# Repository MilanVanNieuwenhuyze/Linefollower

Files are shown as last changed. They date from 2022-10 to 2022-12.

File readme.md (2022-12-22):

# LineFollower
<br />
lege repository die je als template kan gebruiken om een eigen repository te starten voor uw linefollower project
<br />
<br />
(https://user-images.githubusercontent.com/114940508/209196277-916155c1-5bc2-4fb1-94a1-3e10acf964d6.jpg)

<br />
<br />
  
## specifications
<br />
microcontroller: Arduino UNO
<br />
motors: DC 50:1 gearmotor
<br />
h-bridge: DRV8835
<br />
sensors: QTR-8A
<br />
batteries: 2x Lithium batterijen 3.7V 3200 mAh
<br />
wireless communication: HC-05
<br />
distance sensor - motors: 8.6 cm
<br />
weight: 0.219 kg
<br />
speed: 0.546 m/s
<br />

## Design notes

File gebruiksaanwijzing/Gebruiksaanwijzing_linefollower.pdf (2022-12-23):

Jarno Calmeyn & Milan Van Nieuwenhuyze

## Gebruiksaanwijzing

Voorzie de linefollower van stoom:

Optie 1: met de Lithium batterijen

- Maak dat de Robot losgekoppeld van de computer
- Plaats de twee opgeladen lithium batterijen in de houder achteraan op de Robot
- Zet de schakelaar zodat de led brandt
- De Arduino is nu voorzien van stroom

Optie 2: kabel via computer

- Controleer dat het ledlampje niet brand (haal voor de zekerheid de batterijen uit de Robot)
- Verbind de Robot met de computer via de meegeleverde kabel (USB B)
- Het ledlampje zal branden en de arduino is nu voorzien van stroom

Opstarten van de Linefollower

- Koppel de robot los van de USB type B kabel
- Plaats (indien nog niet aanwezig) de twee lithium batterijen in de daar voor voorziene houder volgens de instructies aangegeven op de houder (plus aan plus en min aan min)
- Zet de schakelaar aan zodanig de led brandt
- Zet de robot op het zwarte vlak op het parcour
- Kalibreer zwart via de Seriële monitor ‘Start calibrating black’
- Zet de robot op het wit gedeelte op het parcour
- Kalibreer wit via de Seriële monitor ‘start calibrating white’
- De robot is nu klaar voor gebruik

Rijden met de linefollower

- Plaats de robot op het parcour op de startplaats
- Druk op de start/stop knop
- De robot zal de lijn op het parcour beginnen volgen
- Voor te stoppen pak je de robot van het parcour (hij zal automatisch stoppen met rijden)

Uitschakelen van de Linefollower

- Zet de schakelaar zodanig de led niet brandt
- Haal voor de zekerheid de lithium batterijen uit de houder

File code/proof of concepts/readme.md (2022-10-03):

# Proof of Concepts

Een proof of concept is een combinatie van minimale hard- en software om eenvoudig aan te tonen dat iets werkt.  
Proof of concepts kunnen enerzijds als eerste poging dienen om een bepaald onderdeel van het project werkend te krijgen. Anderzijds kunnen ze tijdens het debuggen van het finale project dienen als test om eventuele hardware problemen te elimineren bij onduidelijke problemen.
<br />  
<br />
Een proof of concept bestaat uit
* een elektronisch schema (indien van toepassing)
* minimale code om de voorop gestelde zaken te demonstreren
* minimale uitleg / aandachtspunten
<br />
De elektronische schakelingen van de proof of concepts komen bij voorkeur overeen met deze van de uiteindelijke linefollower, zodat de code zonder aanpassingen op het finale project kan draaien.

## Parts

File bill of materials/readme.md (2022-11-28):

## bill of materials
<br />

|volgnummer|naam|omschrijving|nieuw/recup|kostprijs/stuk|aantal|subtotaal|
|---|----|---|---|---|---|---|
| 1|  Arduino uno  |  De Arduino UNO zal er voor zorgen dat we alle onderdelen kunnen aansturen aan de hand van een geschreven code in het programma Arduino IDE |  recup | €0,00 |  1 |  1 |
|2|Batterijhouder (2 x 18650)|In deze houder kunnen we de 2 batterijen plaatsen|recup|€0,00|1|1|
|3|Batterij (2 x 18650) + oplader|Deze batterijen zullen alle onderdelen van voeding voorzien|recup|€0,00|1|1|
|4|DC 50:1 gearmotor|De motoren zullen ervoor zorgen dat de wielen beginnen draaien|nieuw|€18,35|2|€36,70|
|5|H-brug (DRV8835)|De H-brug zal de draaizin en snelheid van de motoren regelen|nieuw|€7,15|1|€7,15|
|6|Array sensor (QTR-8A)|De sensor zal de zwarte lijn op het parkour detecteren, zo zal de robot deze lijn blijven volgen|nieuw|€11,5|1|€11,5|
|7|Bluetooth module (HC-05)|De bleutooth module zal er voor kunnen zorgen dat we draadloos met de robot kunnen communiceren, dit aan de hand van een app op de gsm|nieuw|€6,85|1|€6,85|
|8|Polulu wiel (40 x  7) zwart|Wielen, hierdoor zal de robot kunnen rijden op een oppervlakte|nieuw|€2,48|2|€4,96|
|9|Gearmotor bracket|Houdertjes die aan de grondplaat worden bevestigd, deze zorgen ervoor dat de motoren op hun plaats blijven|nieuw|€1,98|2|€3,96|
|10|Tuimelschakelaar|Schakelaar voor de robot van voeding te voorzien|recup|€0,00|1|€0,00|
|11|Dupont draadjes|Verbinden van ingangen en uitgangen|recup|€0,00|15|€0,00|
|12|Drukknop|Zet het karretje aan/uit|recup|€0,00|1|€0,00|
|13|Led|Geeft aan of de voeding aan staat|recup|€0,00|1|€0,00|
|14|Bouten|Houdt de onderdelen op zijn plaats|recup|€0,00|10|€0,00|
| | | | | |Totaal |€71,10 |

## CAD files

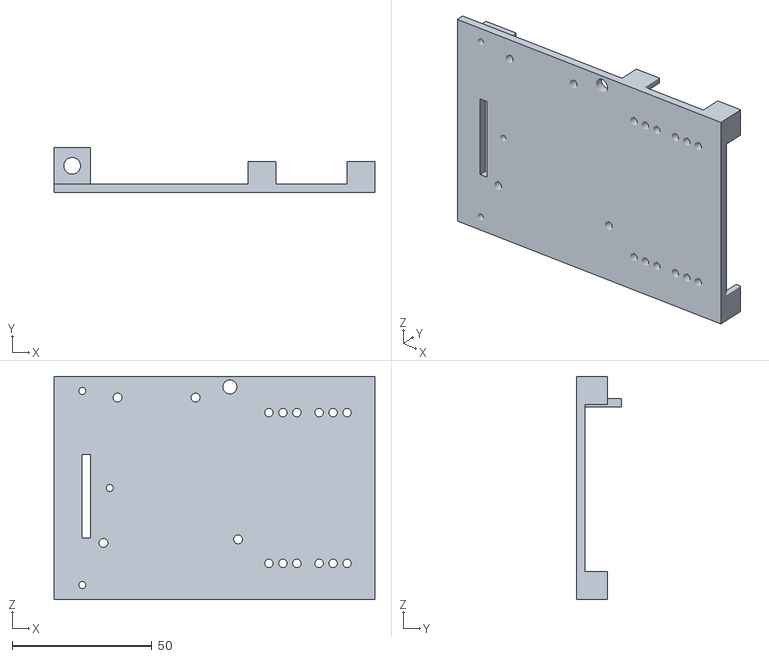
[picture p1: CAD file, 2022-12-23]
technische tekeningen/mechanisch/Bodemplaat.STL
115.0 x 16.0 x 80.0

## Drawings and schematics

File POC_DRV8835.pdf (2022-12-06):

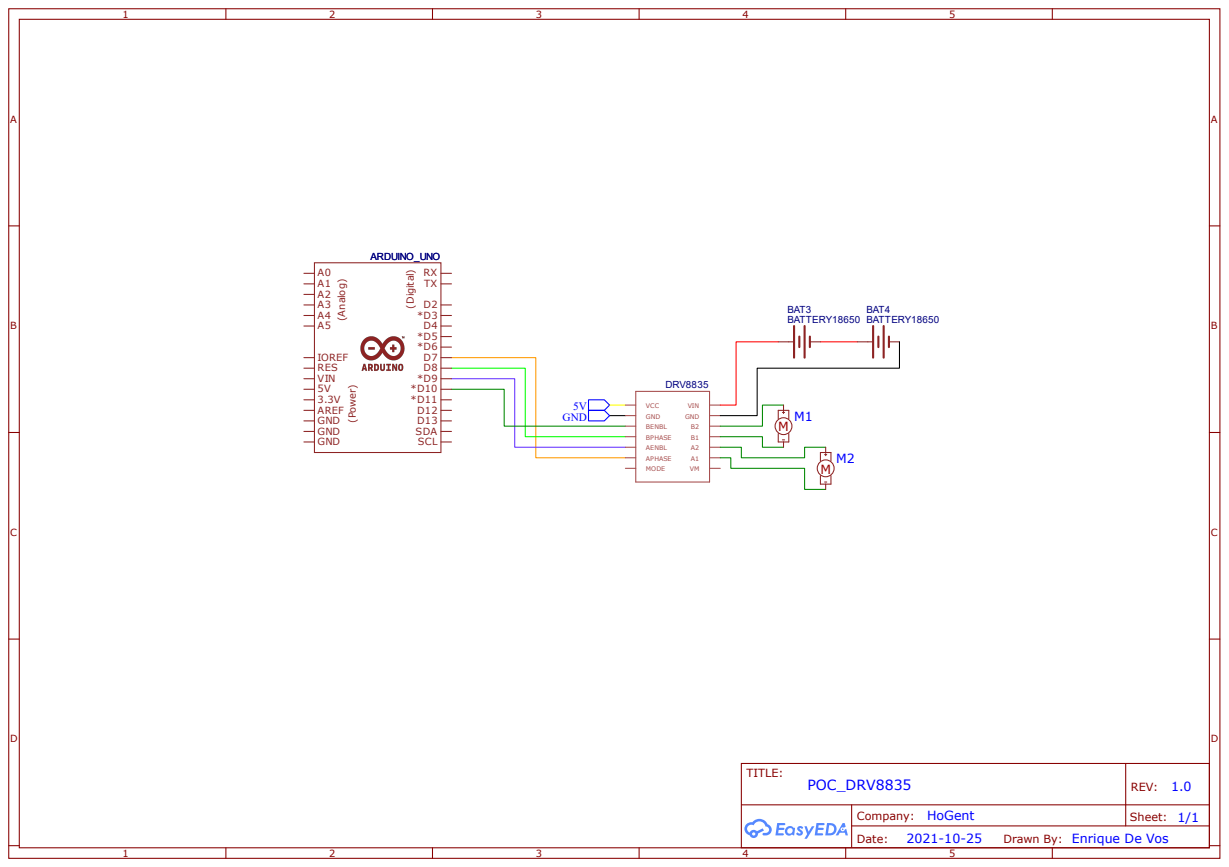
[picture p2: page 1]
TITLE:; POC_DRV8835; REV: 1.0; Date:; Sheet: 1/1; Company: HoGent; ARDUINO_UNO; GND; DRV8835; GND BENBL BPHASE; MODE; VCC; VIN; AENBL; APHASE; ARDUINO_UNO RX TX; RES; AREF GND GND GND; IOREF; SDA SCL; (Analog); (Digital); (Power); BATTERY18650; BAT3; BAT4

Drawn By: Enrique De Vos

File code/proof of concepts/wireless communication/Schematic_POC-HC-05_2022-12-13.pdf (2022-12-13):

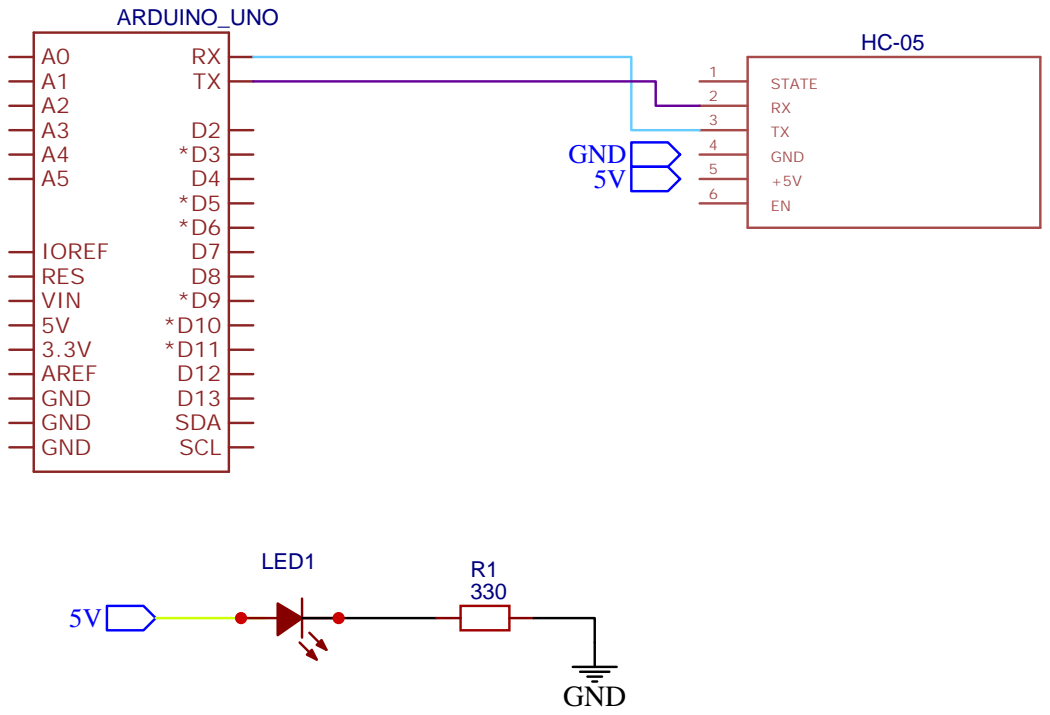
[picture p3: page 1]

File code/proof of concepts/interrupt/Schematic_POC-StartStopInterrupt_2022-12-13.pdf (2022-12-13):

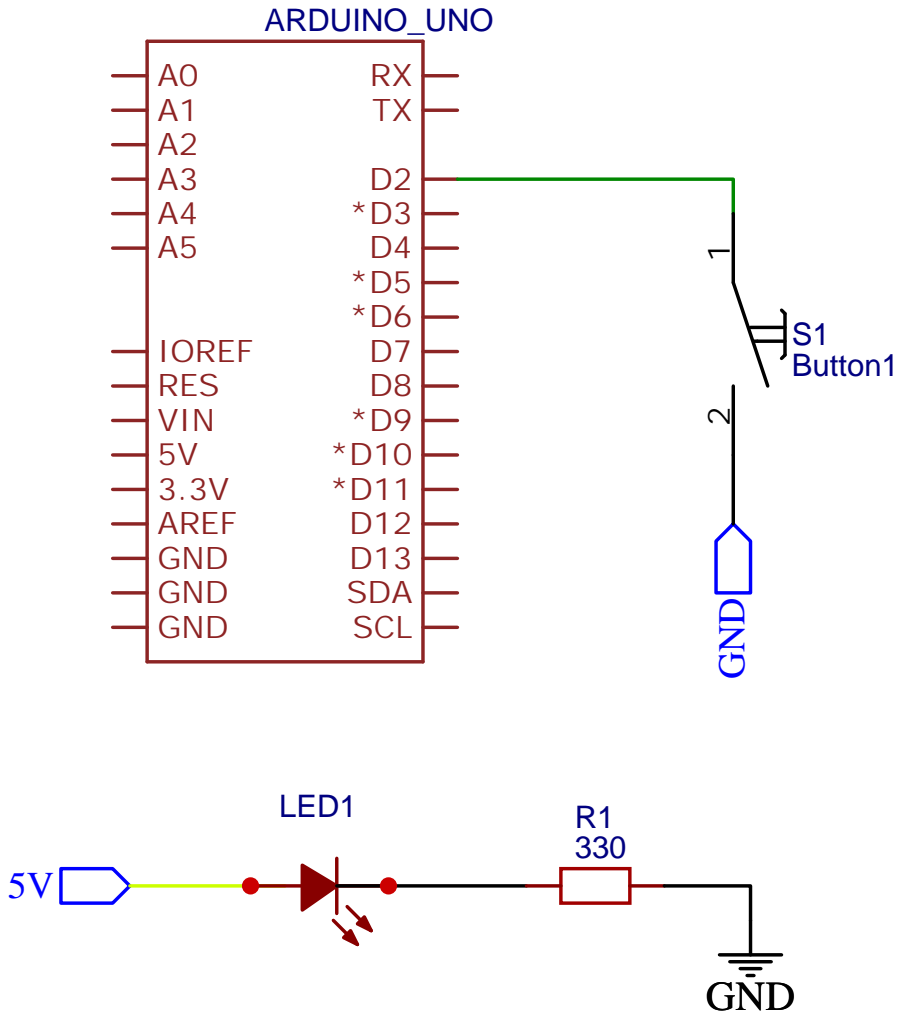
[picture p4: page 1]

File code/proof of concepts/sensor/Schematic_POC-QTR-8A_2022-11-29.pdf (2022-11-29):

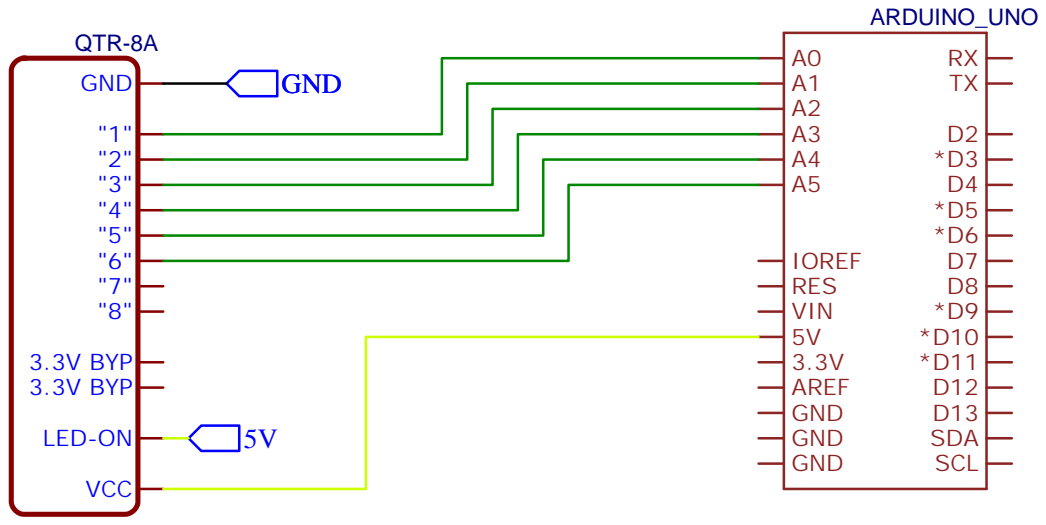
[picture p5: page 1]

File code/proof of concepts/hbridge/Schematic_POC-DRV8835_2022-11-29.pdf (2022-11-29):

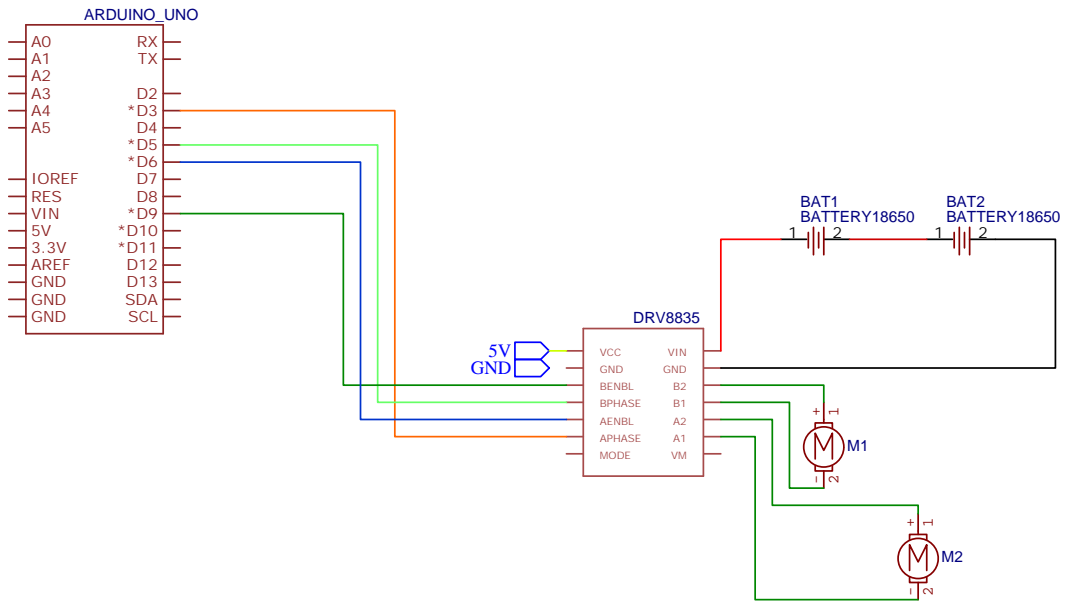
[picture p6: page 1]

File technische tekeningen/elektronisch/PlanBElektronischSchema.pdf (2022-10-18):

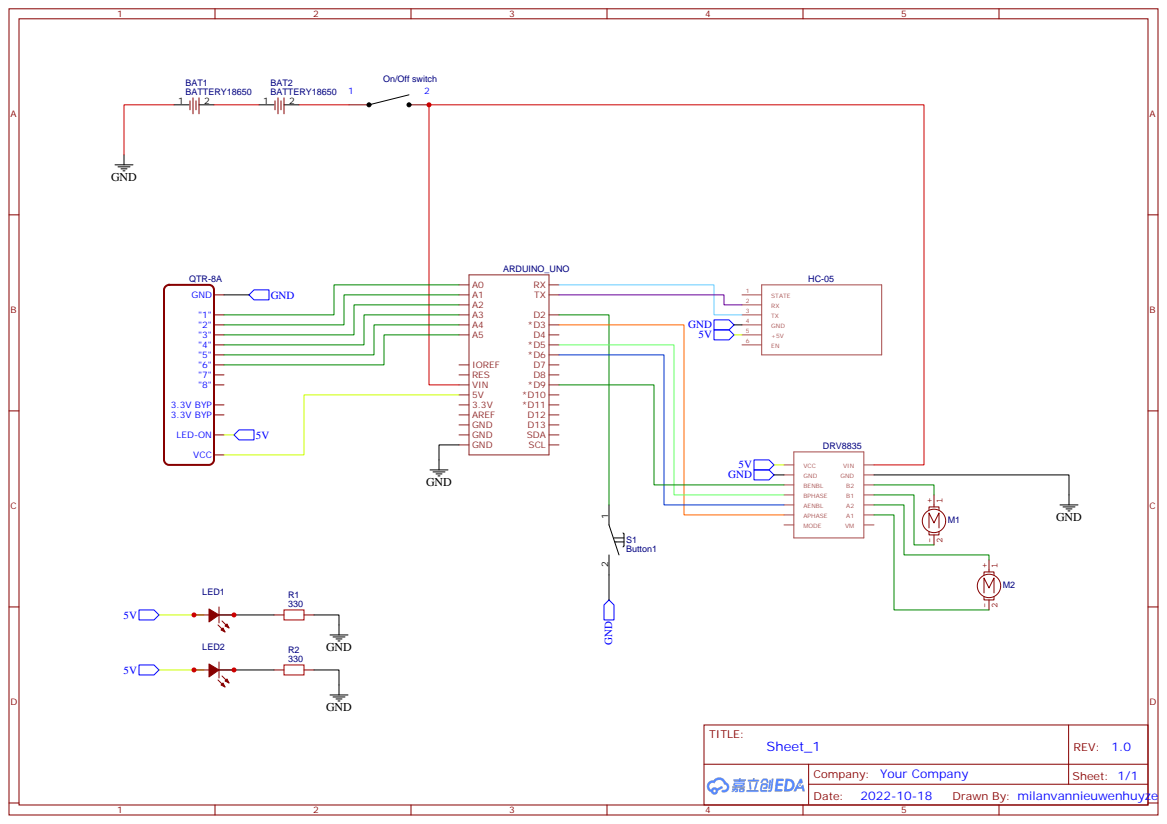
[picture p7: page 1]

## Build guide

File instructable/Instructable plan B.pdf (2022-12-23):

Milan Van Nieuwenhuyze & Jarno Calmeyn

## Instructable plan B

1. Benodigdheden

Open de Bill of Materials, hierin staan alle componenten die nodig zijn om de linefollower plan B te maken. Bestel deze componenten. We hebben nog een paar extra componenten nodig die niet in de Bill of Materials staan. De bodemplaat is gemaakt met een 3D-printer, deze kan u aankopen of u vindt iemand die u deze ter beschikking kan stellen.

Voor de assemblage zal u ook een paar extra componenten nodig hebben, namelijk een soldeerbout, jumper kabels, bouten en moeren.

Voor het programma te schrijven op de arduino zal u de software van arduino moeten
installeren | op | uw | computer. | Deze | kan | u | vinden | op | hun | website,
https://www.arduino.cc/en/software. Voor de computer te verbinden met de arduino zal u een bijpassende kabel nodig hebben.
2. Voorbereiding

Voor we kunnen beginnen aan de assemblage van de onderdelen zullen we nog enkele voorbereidingen moeten treffen alsook het testen van de componenten. Via de Proof of Concepts kan u de benodigde bestanden vinden, zowel het elektronisch schema als het geprogrameerd arduino bestand, om te testen of de componenten effectief werken.
2.1 Bodemplaat

Bij technische tekeningen – mechanisch is een STL bestand van de bodemplaat toegevoegd. Open dit bestand en stuur dit door naar de gewenste 3D-printer. Als uw bodemplaat klaar is kan het zijn dat deze nog niet perfect is. U kan eventueel schuurpapier gebruiken of een boormachine om de gaten beter te maken.
2.2 H-brug (DRV8835)

Voor we de H-brug assembleren op de arduino is het beter om eerste de pinnen in de juiste poorten te steken. Zo kunnen de pinnen rechter gesoldeerd worden. De H-brug kan er later nog overgeschoven worden. De ene kant heeft 4 pinnen en de andere kan heeft 5 pinnen. Steek de kant met 5 pinnen in de digitale ouputs 6,7,8,9 en 10. De kant met 4 pinnen steek je in de bijhorden poorten, namelijk Vin, GND, GND, 5V. Schuif nu het motorshield over de pinnen en soldeer vast. Zorg ervoor dat de opening van de blauwe connectoren langs de buitenkant zit. Dit zal nodig zijn voor latere assemblage.
2.3 Motors & wielen

U soldeert aan de achterkant van de motors op de voorziene klemmen draden. Dit zijn er twee per motor. Schuif op de assen van de motoren de wielen.

2.4 Sensor (QTR-8A)

Soldeer de pinnen op de sensor. Soldeer op poort 1 t.e.m 8. Soldeer ook de poorten GND, LEDON en VCC. De sensoren moeten zich onderaan bevinden en de pinnen bovenaan.
2.5 Start/Stop drukknop

Soldeer hier ook 2 draden aan de voorziene aansluitingen. Deze zullen we later aan de arduino bevestigen.

3. Assemblage

De assemblage is het laatste deel van de instructable om de linefollower na te bouwen.
3.1. Motoren + wielen

De motoren en wielen zullen gemonteerd worden op de onderkant van de bodemplaat. Monteer de motorbrackets op de juiste plaat. De nodige gaten zijn hiervoor voorzien. Gebruik bouten en moeren om de brackets vast te zetten. Laat nog wat speling over en plaats de motoren in de brackets met die wielen langs de buitenkant. Draai de bouten en moeren nu volledig vast. Steek de kabels van de motoren door het voorziene gat in het midden van de bodemplaat.
3.2 Aan/uit schakelaar

Bevestig de aan/uit schakelaar aan de batterijhouder. Soldeer de rode en zwarte draad van de batterijhouder aan de meest linkse pinnen van de schakelaar.

Soldeer op de middenste pinnen van de schakelaar een rode en zwarte draad. Deze sluiten we later op de H-brug aan.

Steek de schakelaar door het gat vooraan de bodemplaat. Zet deze vervolgens vast met bout en moer. Aan de achterkant van de bodemplaat kunnen we da batterijhouder steken. U kan deze eventueel lijmen voor extra stevigheid.
3.3 Start/stop drukknop

Sluit de gesoldeerde draden aan op de arduino. Doet dit op pin 3 en op ground. Als u extra stevigheid wilt lijmt u de knop rechts van de sensor vooraan.
3.4 Sensor

Steek de pinnen op de sensor door de voorziene gleuf vooraan de bodemplaat. Zet de sensor met bouten en moeren vast. Soldeer draadjes aan de pinnen van de middenste sensoren. Deze zullen later bevestig worden aan de analoge ingangen van de arduino.

Aangezien we de grounds mogen doorverbinden, gaan we aan de onderkant van de bodemplaat alle kabels die aan de ground van de arduino komen, verbinden met elkaar. Dit kan u eventueel met krimpkous doen.

3.5 Ground met arduino verbinden

Verbind de samengenomen grounds met de arduino. Soldeer het uiteinde van de draden aan de kleine pinnen onderaan de arduino.
3.6 Arduino

De arduino met bijhorden H-brug op, monteren we op de bodemplaat. Zet deze vast doormiddel van bouten en moeren. Als dit goed gedaan is zullen de kabels onder de arduino kunnen liggen, en zullen deze zo goed als onzichtbaar zijn.

Sluit de 6 draden van de sensor aan op pin A0-A5 van de arduino. De draad van de drukknop sluiten we aan op pin 3.

Sluit de 2 draden van de rechtse motor aan op de B-klemmen van de H-brug. Sluit de 2 draden van de linkse motor aan op de A-klemmen van de H-brug. De voeding van de schakelaar sluiten we aan op de overige klemmen van de H-brug.

4. Compileren

Nu we de linefollower succesvol in elkaar gestoken hebben, zullen we het arduino programma nog moeten opladen op de arduino, zodat deze correct de zwarte lijn kan volgen.

Open het arduino project onder finale code. Verbind de arduino met bijhorende kabel met de computer. Ga bovenaan in het arduino project naar ‘hulpmiddelen’ →’board’ en selecteer Arduino Uno. Vervolgens ga je naar ‘poort’. Dit staat onder ‘board’. Selecteer de juist COM poort waarmee de arduino verbonden is. Nu is het programma klaar om op de arduino geladen te worden. Klik links bovenaan op het ronde symbool ‘verifiëren’. Even wachten en klik tenslotte op het symbool rechts van ‘verifiëren’, genaamd ‘uploaden’. Als alles goed gegaan is, zou het programma nu op de arduino moeten staan.

5. Starten

Flip de schakelaar aan, u zou een lampje moeten zien branden als er voeding is. Nu de linefollower voorzien is van voeding kan u deze het parcours laten rijden. Download een van de parcours op juiste grootte en plaats de linefollower op de zwarte lijn. Als u nu de drukknop korstondig induwt zal de linefollower beginnen rijden en de zwarte lijn volgen.

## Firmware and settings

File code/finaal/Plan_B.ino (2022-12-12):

#include "SerialCommand.h"
#include "EEPROMAnything.h"

#define SerialPort Serial
#define Baudrate 9600

#define rotationL 7
#define rotationR 8
#define speedM1 9
#define speedM2 10

const byte StartStop = 3;

float iTerm = 0;
float lastErr = 0;

SerialCommand sCmd(SerialPort);
bool debug;
unsigned long previous, calculationTime;
bool run = false;

const int sensor[] = {A0, A1, A2, A3, A4, A5};
struct param_t
{
  unsigned long cycleTime;
  int black[6];
  int white[6];
  int power;
  float diff;
  float kp;
  float ki;
  float kd;
 } params;

void setup()
{
  SerialPort.begin(Baudrate);

  sCmd.addCommand("set", onSet);
  sCmd.addCommand("calibrate", onCalibrate);
  sCmd.addCommand("debug", onDebug);

  sCmd.setDefaultHandler(onUnknownCommand);

  EEPROM_readAnything(0, params);

  pinMode(13, OUTPUT);
  SerialPort.println("ready");

  pinMode(StartStop, INPUT_PULLUP);
  attachInterrupt(digitalPinToInterrupt(StartStop), ProgrammaRun , FALLING);
}

void loop()
{
  sCmd.readSerial();

  unsigned long current = micros();
  if (current - previous >= params.cycleTime)
  {
    previous = current;

    int normalised[6];

    for (int i = 0; i < 6; i++)
    {
      normalised[i] = map(analogRead(sensor[i]), params.black[i], params.white[i], 0, 1000);

    }


    /* interpolatie */
    int index = 0;
    float position;
    for (int i = 1; i < 6; i++) if (normalised[i] < normalised[index]) index = i;

    if (normalised[index] > 700) run = false;

    if (index == 0) position = -30;
    else if (index == 5) position = 30;
    else
    {
      int sNul = normalised[index];
      int sMinEen = normalised [index - 1];
      int sPlusEen = normalised[index + 1];

      float b = sPlusEen - sMinEen;
      b = b / 2;

      float a = sPlusEen - b - sNul;

      position = -b / (2 * a);
      position += index;
      position -= 2.5;

      position *= 9.525;
    }

    /* Proportionele regelaar */
    
    float error = -position;
    float output = error * params.kp;

    /* Integrerend */

    iTerm += params.ki * error;
    iTerm = constrain(iTerm, -510, 510);
    output += iTerm;

    /* Differentiërend */

    output += params.kd * (error - lastErr);
    lastErr = error;

    output = constrain(output, -510, 510);


    if (run)
    {

      int powerLeft = 0;
      int powerRight = 0;

      if (output >= 0)
      {
        powerLeft = constrain(params.power + params.diff * output, -255, 255);
        powerRight = constrain(powerLeft - output, -255, 255);
        powerLeft = powerRight + output;
      }
      else

      {
        powerRight = constrain(params.power - params.diff * output, -255, 255);
        powerLeft = constrain(powerRight + output, -255, 255);
        powerRight = powerLeft - output;
      }

      if (powerRight < 0) digitalWrite(rotationR, LOW);
      if (powerRight > 0) digitalWrite(rotationR, HIGH);
      if (powerLeft < 0) digitalWrite(rotationL, LOW);
      if (powerLeft > 0) digitalWrite(rotationL, HIGH);

      analogWrite(speedM1, abs(powerRight));
      analogWrite(speedM2, abs(powerLeft));
    }
    else  // run = false;
    {

      digitalWrite(rotationR, LOW);
      digitalWrite(rotationL, LOW);

      analogWrite(speedM1, 0);
      analogWrite(speedM2, 0);
    }

  }

  unsigned long difference = micros() - current;
  if (difference > calculationTime) calculationTime = difference;
}

void onUnknownCommand(char *command)
{
  SerialPort.print("unknown command: \"");
  SerialPort.print(command);
  SerialPort.println("\"");
}

void ProgrammaRun() {
  run = ! run;
  iTerm = 0;
  lastErr = 0;
}

void onSet()
{
  char* param = sCmd.next();
  char* value = sCmd.next();

  if (strcmp(param, "cycle") == 0)
  {
    params.cycleTime = atol(value);
    long newCycleTime = atol(value); 
    float ratio = ((float) newCycleTime) / ((float) params.cycleTime);

    params.ki *= ratio;
    params.kd /= ratio;

    params.cycleTime = newCycleTime;

  }

  else if (strcmp(param, "ki") == 0)
  {
    float cycleTimeInSec = ((float) params.cycleTime) / 1000000;
    params.ki = atof(value) * cycleTimeInSec;
  }

  else if (strcmp(param, "kd") == 0)
  {
    float cycleTimeInSec = ((float) params.cycleTime) / 1000000;
    params.kd = atof(value) / cycleTimeInSec;
  }
  else if (strcmp(param, "run") == 0) run = atol(value);
  else if (strcmp(param, "power") == 0) params.power = atol(value);
  else if (strcmp(param, "diff") == 0) params.diff = atof(value);
  else if (strcmp(param, "kp") == 0) params.kp = atof(value);

  EEPROM_writeAnything(0, params);
}

void onDebug()
{
  SerialPort.print("cycle time: ");
  SerialPort.println(params.cycleTime);

  SerialPort.print("black: ");
  for (int i = 0; i < 6; i++) {
    SerialPort.print(params.black[i]);
    SerialPort.print(" ");
  }
  SerialPort.println(" ");

  SerialPort.print("white: ");
  for (int i = 0; i < 6; i++) {
    SerialPort.print(params.white[i]);
    SerialPort.print(" ");
  }
  SerialPort.println(" ");

  SerialPort.print("kp: ");
  SerialPort.println(params.kp);

  float cycleTimeInSec = ((float) params.cycleTime) / 1000000;
  float ki = params.ki / cycleTimeInSec;
  SerialPort.print("Ki: ");
  SerialPort.println(ki);

  float kd = params.kd * cycleTimeInSec;
  SerialPort.print("Kd: ");
  SerialPort.println(kd);

  SerialPort.print("diff: ");
  SerialPort.println(params.diff);

  SerialPort.print("power: ");
  SerialPort.println(params.power);

  SerialPort.print("calculation time: ");
  SerialPort.println(calculationTime);
  calculationTime = 0;
}


void onCalibrate()
{
  char* param = sCmd.next();

  if (strcmp(param, "black") == 0)
  {
    SerialPort.print("start calibrating black... ");
    for (int i = 0; i < 6; i++) params.black[i] = analogRead(sensor[i]);
    SerialPort.println("done");
  }
  else if (strcmp(param, "white") == 0)
  {
    SerialPort.print("start calibrating white... ");
    for (int i = 0; i < 6; i++) params.white[i] = analogRead(sensor[i]);
    SerialPort.println("done");
  }

  EEPROM_writeAnything(0, params);
}

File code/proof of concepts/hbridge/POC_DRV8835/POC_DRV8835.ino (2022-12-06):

#include <DRV8835MotorShield.h>

DRV8835MotorShield motors;

void setup()
{ }

void loop()
{
  
  // run M1 motor with positive speed
  
  
  
  for (int speed = 0; speed <= 255; speed++)
  {
    motors.setM1Speed(speed);
    delay(2);
  }

  for (int speed = 255; speed >= 0; speed--)
  {
    motors.setM1Speed(speed);
    delay(2);
  }
  
  // run M1 motor with negative speed
  
  
  
  for (int speed = 0; speed >= -255; speed--)
  {
    motors.setM1Speed(speed);
    delay(2);
  }
  
  for (int speed = -255; speed <= 0; speed++)
  {
    motors.setM1Speed(speed);
    delay(2);
  }

  // run M2 motor with positive speed
  
  
  
  for (int speed = 0; speed <= 255; speed++)
  {
    motors.setM2Speed(speed);
    delay(2);
  }

  for (int speed = 255; speed >= 0; speed--)
  {
    motors.setM2Speed(speed);
    delay(2);
  }
  
  // run M2 motor with negative speed
  
 
  for (int speed = 0; speed >= -255; speed--)
  {
    motors.setM2Speed(speed);
    delay(2);
  }
  
  for (int speed = -255; speed <= 0; speed++)
  {
    motors.setM2Speed(speed);
    delay(2);
  }

  // run M1 and M2 motor with positive speed

  for (int speed = 0; speed <= 255; speed++)
  {
    motors.setM1Speed(speed);
    motors.setM2Speed(speed);
    delay(2);
  }

  for (int speed = 255; speed >= 0; speed--)
  {
    motors.setM1Speed(speed);
    motors.setM2Speed(speed);
    delay(2);
  }
  
  // run M1 and M2 motor with negative speed
  
  
  
  for (int speed = 0; speed >= -255; speed--)
  {
    motors.setM1Speed(speed);
    motors.setM2Speed(speed);
    delay(2);
  }
  
  for (int speed = -255; speed <= 0; speed++)
  {
    motors.setM1Speed(speed);
    motors.setM2Speed(speed);
    delay(2);
  }
  
  delay(500);

}
